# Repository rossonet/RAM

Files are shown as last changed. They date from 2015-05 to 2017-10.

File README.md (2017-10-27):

# Rossonet Atom Machine

Rossonet



[http://www.rossonet.org](http://www.rossonet.org)

Licenza: [LGPL 3.0](https://www.gnu.org/licenses/lgpl.html)
Per maggiori dettagli sulla licenza rimando a [questa voce](http://it.wikipedia.org/wiki/GNU_Lesser_General_Public_License) di Wikipedia

LGPL Logo

Rossonet Atom Machine è una macchina a controllo numerico su 3 assi completamente open source.

La macchina è governabile via rete tramite un browser, il software montato a bordo guida l'utente nelle varie fasi di lavorazioni in un contesto social.

La macchina è composta da parti in plastica derivate da varie versione della [RepRap Rostock](http://reprap.org/wiki/Rostock) e componenti meccaniche (barre rettificate, cuscinetti e cinghie) facilmente reperibili localmente e online. Tutte le parti sono disegnate [con OpenScad](http://www.openscad.org/).

I giunti cardanici sono magnetici, questo permette una rapida sostituzione delle parti, ma anche la sicurezza che, in caso di errore nella programmazione software, la macchina si smonterà senza danneggiarsi o danneggiare qualcuno o qualcosa.
 
L'elettronica di controllo è una [Megatronics V3](http://reprapworld.com/mt/megatronics3_src.zip), architettura che integra in un'unica scheda il progetto Arduino Mega e il progetto RAMPS. La scheda monta un processore Atmega2560 a 16MHz.

L'elettronica è governata dal [firmware Marlin](https://github.com/MarlinFirmware/Marlin).

Alla scheda di controllo è collegato un computer embedded con processore A20. Sui protipi è montata una scheda [BananaPI](http://www.bananapi.org/).

Oltre ad una distribuzione Linux ottimizzata per la scheda specifica -Fedora 22-, il computer offre le fuzionalità di controllo web tramite [OctoPrint](http://octoprint.org/); la virtualizzazione della seriale, per usare la macchina come una CNC con programmi come [Printrun](https://github.com/kliment/Printrun) o [LinuxCNC](http://sourceforge.net/projects/emc/); le funzionalità di slicing per la stampa plastica sono gestite con [CuraEngine](https://github.com/Ultimaker/CuraEngine); le funzionalità CAD con [OpenJSCAD](https://github.com/Spiritdude/OpenJSCAD.org/wiki/User-Guide); il CAM (calcolo dei percorsi di incisione o scrittura) con [PyCAM](http://pycam.sourceforge.net/).

L'interfaccia web è fruibile da dispositivo mobile grazie alla libreria [Twitter Bootstrap](http://getbootstrap.com/2.3.2/).

<a href="http://www.youtube.com/watch?feature=player_embedded&v=1BcRuSaGWxI" target="_blank">Rossonet</a>

## Funzionalità
1. stampa 3D a filamento fuso (1,75mm) con temperatura di lavorazione fino 240 gradi (PLA,ABS,ecc...);
2. attuatore per eseguire GCODE con penne, matite, pennarelli, ecc...;
3. interfaccia web responsible;
4. taglio polistirolo -da implementare-;
5. piano di lavoro riscaldato con aggancio magnetico -da implementare-;
6. attuatore a siringa per la lavorazione di materiali liquidi -da implementare-;
7. help Online integrato nell'interfaccia per imparare con il supporto multimediale come utilizzare e svolgere le procedure di manutenzione della macchina -in sviluppo-. In particolare le procedure di calibrazione della struttura, calibrazione del termostato, cambio filamento, tuning z-probe;
8. sistema di assistenza remoto basato su chat web -integrazione Olark-;
9. integrazione software di modellizazione parametrica con libreria online in OpenJScad -da implementare-;
10. imballaggi per il traporto -da implementare-;
11. API per l'interfaccia di software di terze parti;
12. integrazione MQTT per il monitoraggio integrato nelle reti IoT -da implementare-;
13. integrazione piattaforma [Rossonet Ar4k](https://github.com/rossonet/agenteAr4k);
14. connessione ethernet o wifi (tramite plug usb);
15. slicing sampa plastica integrato con [CuraEngine](https://github.com/Ultimaker/CuraEngine);
16. timelaps automatico.

## Versioni
Attualmente sistono due versioni preconfigurate della macchina. La versione "T" con le parti meccaniche realizzate in officina di precisione e il modello Eroina studiato per essere realizzabile partendo da stampe plastiche di piccole dimensioni. 

### Versione Eroina (bootstrap progetto)
La versione Eroina è composta da una struttura realizzata in carpenteria (legno, metallo o altre strutture ricavate con il materiale disponibile) e da parti stampate in plastica con sagome inferiori ai 15cm per ogni dimensione. Il nostro primo prototipo è stato stampato con un [Arduino Materia 101](https://www.arduino.cc/en/Main/ArduinoMateria101).

[Schema assemblaggio generale](https://github.com/rossonet/RAM/blob/master/parti/stl/eroina/assemblaggio.stl)

#### Video fasi studio prototipo
studio z-probe
<a href="http://www.youtube.com/watch?feature=player_embedded&v=OmTOs6jjuCw" target="_blank">Rossonet</a>

primi test scheda controllo
<a href="http://www.youtube.com/watch?feature=player_embedded&v=n3oExDMJfP0" target="_blank">Rossonet</a>

primo assemblaggio struttura
<a href="http://www.youtube.com/watch?feature=player_embedded&v=B5Mmt7lzHgg" target="_blank">Rossonet</a>

test usb over ethernet
<a href="http://www.youtube.com/watch?feature=player_embedded&v=iVD2OGaxWTA" target="_blank">Rossonet</a>

esperimenti Marlin
<a href="http://www.youtube.com/watch?feature=player_embedded&v=0e1HDMZBxl4" target="_blank">Rossonet</a>

esperimenti con Marlin
<a href="http://www.youtube.com/watch?feature=player_embedded&v=ZnjUfesXWaY" target="_blank">Rossonet</a>

test GCODE con biglie
<a href="http://www.youtube.com/watch?feature=player_embedded&v=iLzKpcrZ054" target="_blank">Rossonet</a>

primi esperimenti scrittura con pennarello
<a href="http://www.youtube.com/watch?feature=player_embedded&v=tii90TnvsTo" target="_blank">Rossonet</a>

stampa plastica
<a href="http://www.youtube.com/watch?feature=player_embedded&v=GQly_ISp1_0" target="_blank">Rossonet</a>

#### Elenco materiali elettronici, movimentazione lineare e hot end 
1. [E3D v6 HotEnd Full Kit - 1.75mm Universal (Direct) (24v)](http://e3d-online.com/E3D-v6/Full-Kit?product_id=380);
2. ventola raffreddamento 30mmx30mmx10mm 12V;
3. [Banana PI](http://www.bananapi.org/p/product.html);
4. [Megatronics V3](http://reprapworld.com/?products_details&products_id/468/cPath/1591_1643);
5. 4 x [ponti H -DRV8825 Stepper Motor Driver Carrier-](https://www.pololu.com/product/2132);
6. 4 x NEMA17 Stepper motor 1,8 gradi/step - 4,8kg/cm;
7. 3 x [endstop meccanici](http://www.elecfreaks.com/store/images/Mech_Endstop-D.jpg);
8. telecamera USB compatibile con Fedora 22 su Banana PI;
9. servo motore z-probe: 9G micro servo;
10. micro pulsante PCB 3mmx3.5mmx1.8mm button switch (per z-probe);
11. 6 x barre rettificate da 1mt x 12mm;
12. 6 x cuscinetti lineari a sfera LM12UU;
13. cuscinetto piccolo estrusore;
14. cuscinetto grande estrusore;
15. 3 x cuscinetti fine corsa;
13. ~7mt cinghia trasmissione 6mm (GT2 -passo 2mm-);
14. 3 x pulegge alluminio 20 denti (GT2 -passo 2mm-);
15. ~6mt cavo di rete UTP -da utilizzare per i cablaggi-;
16. ~3mt cavo bipolare per resistenza hotend;
17. fascette varie;
18. spinotti per Megatronics v3 (4 stepper, 2 ventole, 3+1 endstop -comprende servo-);
19. alimentatore 12V da PC;
20. scheda SD da 16GB per Banana PI;
21. scheda microSD per memoria tampone scheda controllo;
22. cavo USB da maschio A a maschio B per connessione tra Banana PI e Megatronics v3;
23. terminale maschio micro USB per alimentazione Banana PI. 

#### Elenco materiale stampato
1. 3 x [blocco motore](https://github.com/rossonet/RAM/blob/master/parti/stl/eroina/blocco_motore_v1.stl);
2. 3 x [rimando cinghia](https://github.com/rossonet/RAM/blob/master/parti/stl/eroina/fine_corsa.stl);
3. 3 x [carrello](https://github.com/rossonet/RAM/blob/master/parti/stl/eroina/carrello.stl);
4. 3 x [tensionatore](https://github.com/rossonet/RAM/blob/master/parti/stl/eroina/Belt-Tensioner-V1.stl);
5. 3 x [supporto endstop](https://github.com/rossonet/RAM/blob/master/parti/stl/eroina/supporto_endstop.stl);
6. 1 x [attuatore](https://github.com/rossonet/RAM/blob/master/parti/stl/eroina/piattaforma_3dprint_v2.stl): [base](https://github.com/rossonet/RAM/blob/master/parti/stl/eroina/piattaforma_3dprint_v2_base.stl), [coperchio "A"](https://github.com/rossonet/RAM/blob/master/parti/stl/eroina/piattaforma_3dprint_v2_coperchio_a.stl), [coperchio "B"](https://github.com/rossonet/RAM/blob/master/parti/stl/eroina/piattaforma_3dprint_v2_coperchio_b.stl), [braccio z-probe](https://github.com/rossonet/RAM/blob/master/parti/stl/eroina/piattaforma_3dprint_v2_zprobe.stl);
7. [estrusore](https://github.com/rossonet/RAM/blob/master/parti/stl/eroina/airtripper-extruder-v3.stl);
8. [attuatore pennarelli](https://github.com/rossonet/RAM/blob/master/parti/stl/eroina/piattaforma_giotto_turbocolor.stl) collaudato con "[Giotto Turbocolor](http://www.fila.it/giotto/prodotti/pennarelli/giotto-turbo-color)" con [questo supporto](https://github.com/rossonet/RAM/blob/master/parti/stl/eroina/supporto_giotto_turbocolor.stl).

#### Elenco materiale per struttura e piccola ferramenta
Il progetto di questa versione prevede la predisposizione delle tre colonne attive su una struttura portante realizzata artigianalmente. Lo schema di montaggio generale è visionabile [qui](https://github.com/rossonet/RAM/blob/master/parti/stl/eroina/assemblaggio.stl). La struttura deve garantire una sufficiente rigidità, attenuare le vibrazioni dei movimenti con adeguati piedi e/o ammortizzatori.

La struttura può essere realizzata con diametro a piacere tra i 47 e i 70 centimetri. Al diminuire del diametro proporzianalmete diminuiscono i bracci diagonali dell'attuatore, aumenta l'altezza e diminuisce il raggio utile per la stampa. Per esempio nella [configurazione con raggio di 23,5cm](http://www.rossonet.org/dati/RAM235.html) si ottiene un area di stampa cilindrica con un raggio di 19,5cm e altezza di 43,5cm, i bracci diagonali sono lunghi 395mm. Nella [configurazione con raggio di 35cm](http://www.rossonet.org/dati/RAM350.html) il cilindro utile ha raggio di 31cm e altezza di 20,5cm, i bracci sono lunghi 625mm. 

1. 3 x ferramenta fine corsa;
2. 3 x ferramenta blocco motore;
3. ferramenta attuatore;
4. ferramenta estrusore;
4. 6 x magneti carrello;
5. 12 x magneti attuatore;
6. 12 x sfere acciaio 12mm;
7. 12 x supporti distanziatori in plastica per magneti -da verificare-;
8. 6 x bacchette alluminio diametro 10mm lunghezza da 39,5cm a 62,5cm -a seconda del raggio della struttura portante-;

#### Fasi assemblaggio
-to do-
...con foto in archivio git

#### Servizi
1. download firmware per Banana PI -to do-
2. vendita online modello "T"
3. plastiche "Eroina"
4. elettronica e materiale vario "Eroina"

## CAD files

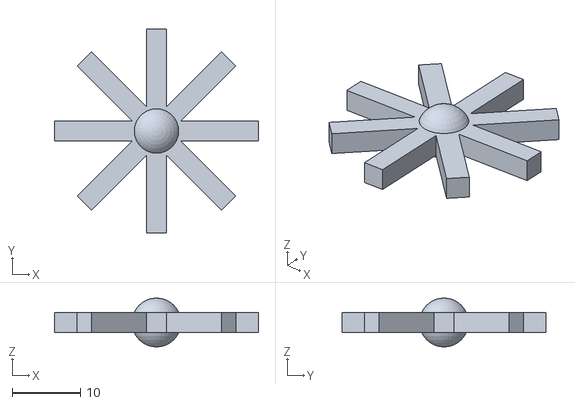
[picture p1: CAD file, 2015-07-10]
OpenJSCAD.org-master/examples/include-test/main.stl
30.0 x 30.0 x 7.20

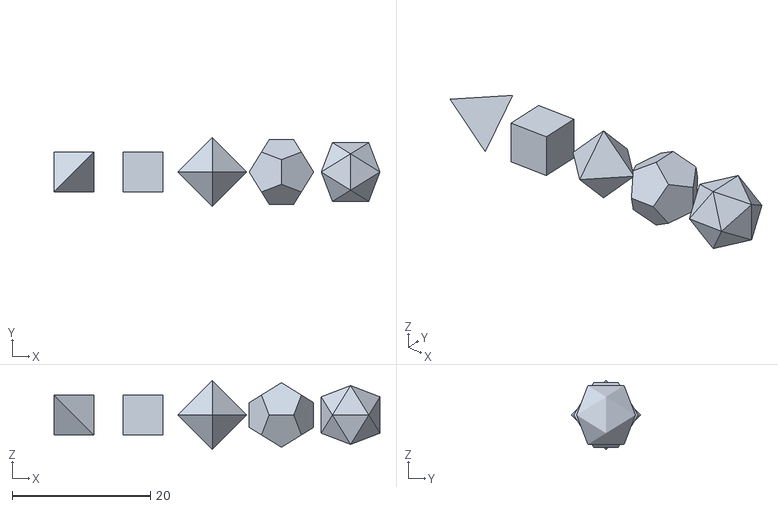
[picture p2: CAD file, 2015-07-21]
OpenJSCAD/examples/platonics/main.stl
47.1 x 10.0 x 10.0

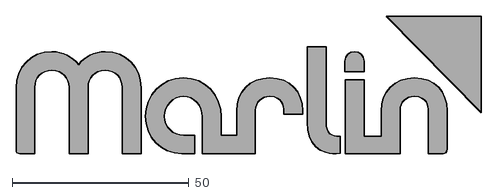
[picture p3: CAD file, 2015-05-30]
Marlin/Documentation/Logo/Marlin Logo.dxf
131.6 x 39.5

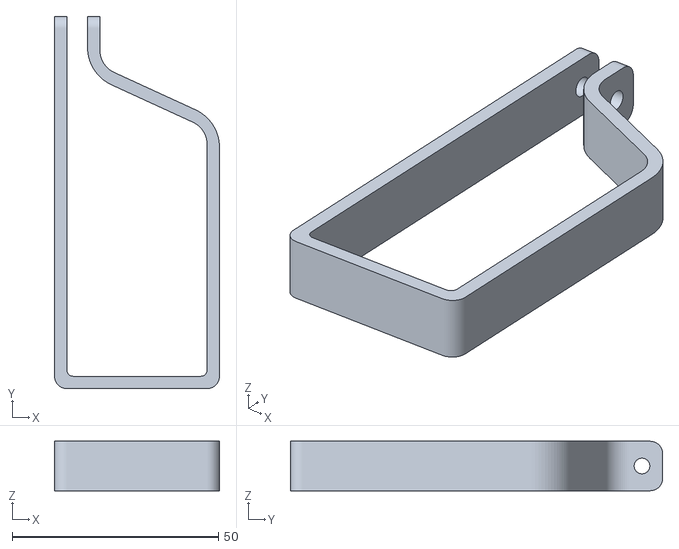
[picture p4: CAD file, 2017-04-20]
modelli/progetti/plotter_a_corde/files/FCE.1501.03.006_batteryholder_side.STL
40.0 x 90.2 x 12.0

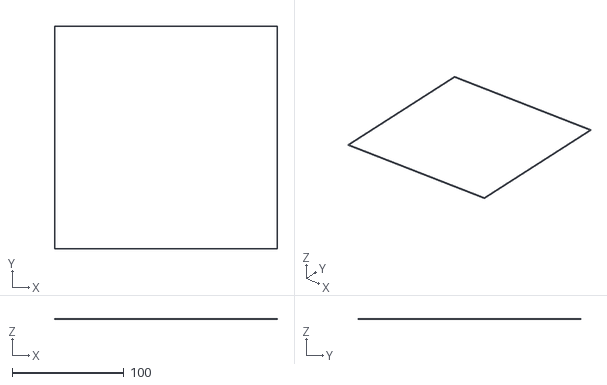
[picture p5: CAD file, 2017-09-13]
modelli/test2d/quadrato_20.stl
200.0 x 200.0 x 1.00

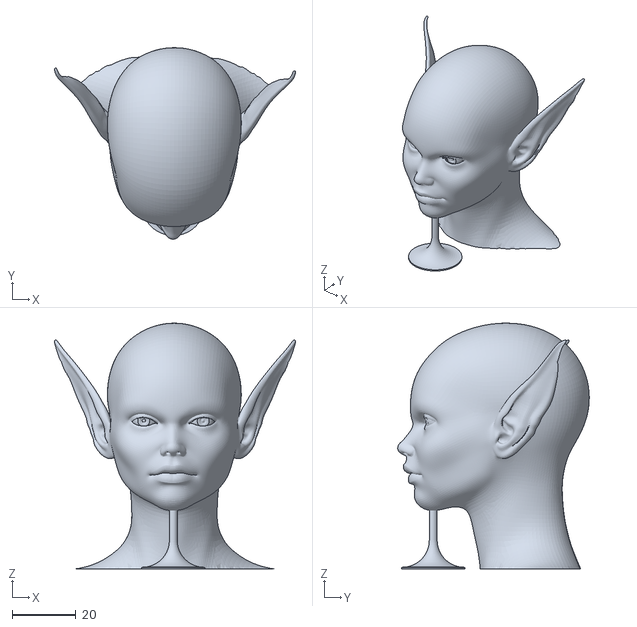
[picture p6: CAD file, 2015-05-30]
modelli/test3d/elfgirl_support_V1.stl
75.8 x 60.3 x 77.3

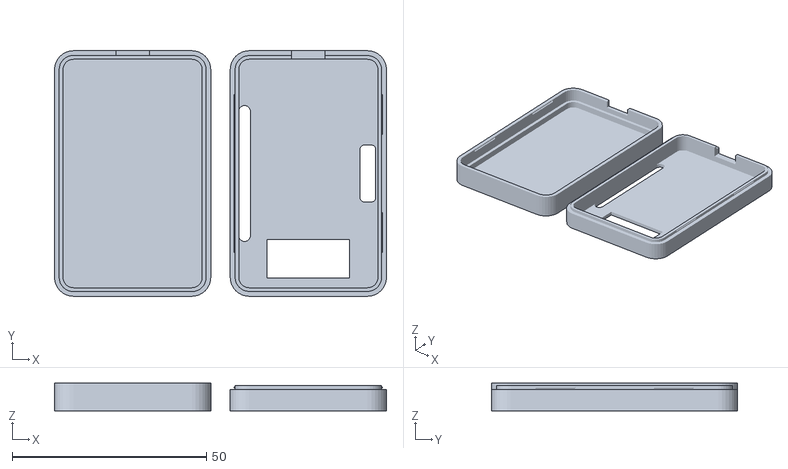
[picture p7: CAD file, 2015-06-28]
OctoPrint/tests/filemanager/_files/bp_case.stl
85.5 x 63.2 x 7.15

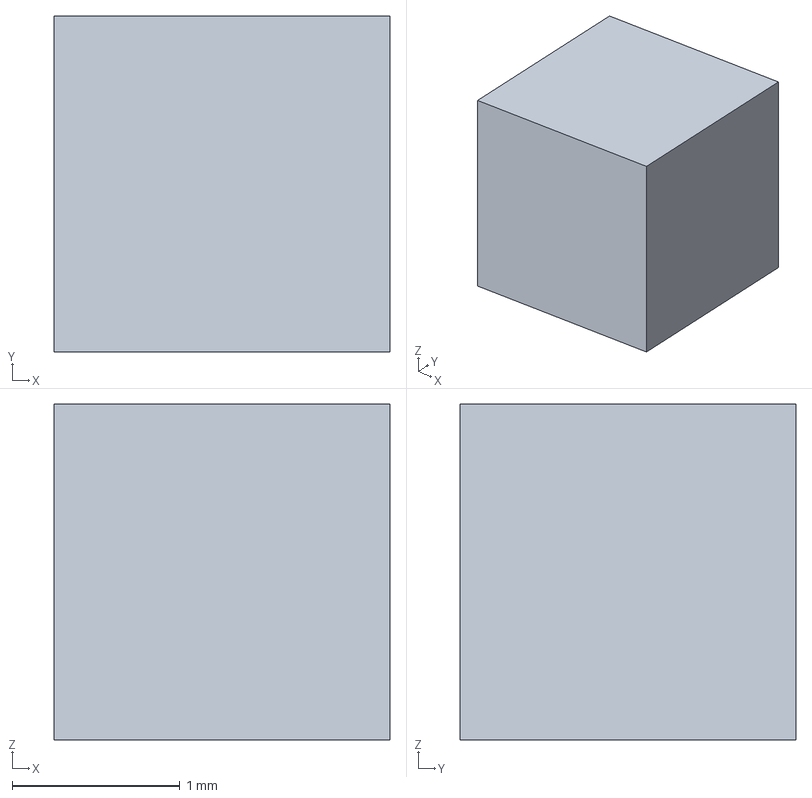
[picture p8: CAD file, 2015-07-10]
OpenJSCAD.org-master/examples/amf/Amf_Cube.amf
2.00 x 2.00 x 2.00 mm

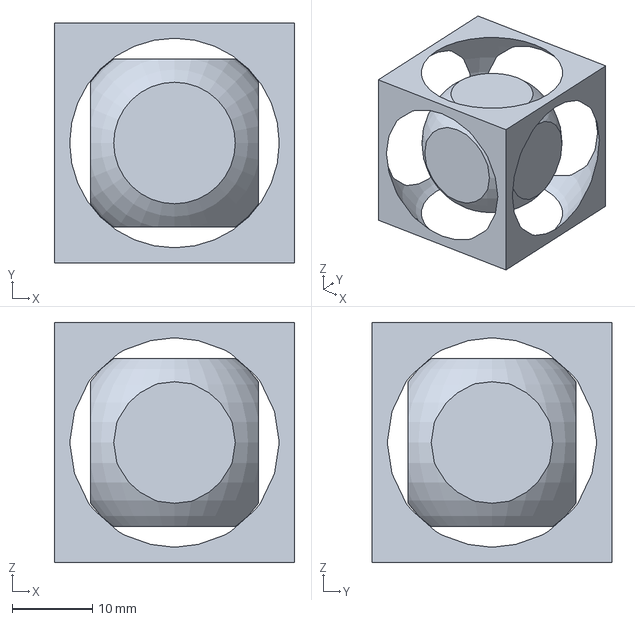
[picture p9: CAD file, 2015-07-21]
OpenJSCAD.org-master/examples/logo.amf
30.0 x 30.0 x 30.0 mm

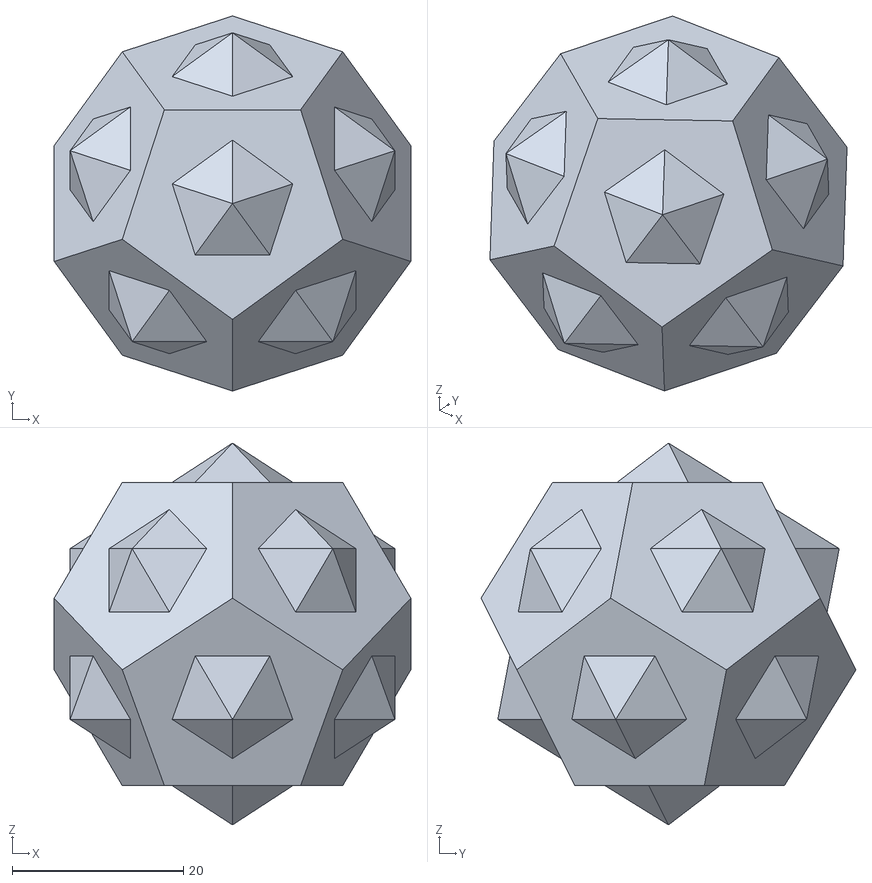
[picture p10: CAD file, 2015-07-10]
OpenJSCAD.org-master/examples/platonics/origv07/dualdodeca_union.stl
41.6 x 43.7 x 44.5

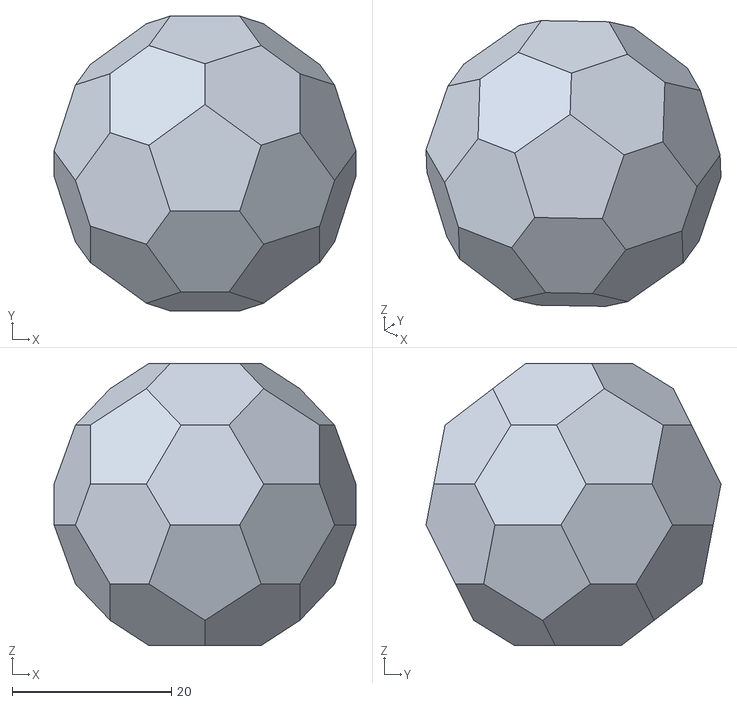
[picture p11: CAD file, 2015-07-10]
OpenJSCAD/examples/platonics/origv07/dualdodeca_intersection.stl
37.9 x 37.0 x 35.4

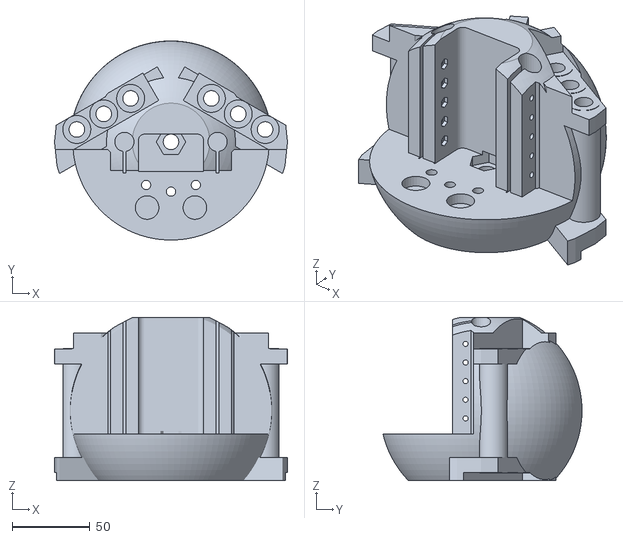
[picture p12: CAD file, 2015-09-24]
parti/stl/piede.stl
150.0 x 128.1 x 105.0

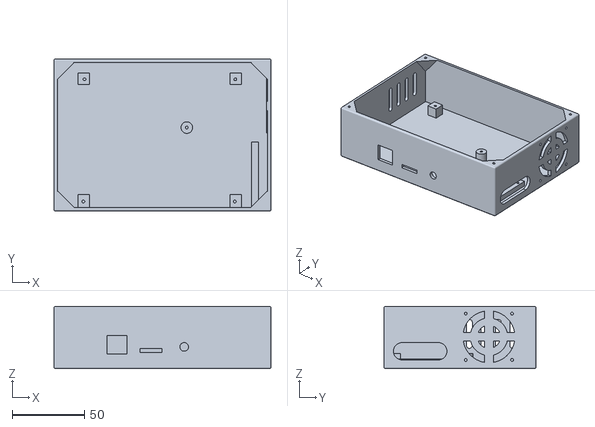
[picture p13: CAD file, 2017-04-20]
RAM/scad/megatronics_case.stl
150.0 x 105.0 x 43.0

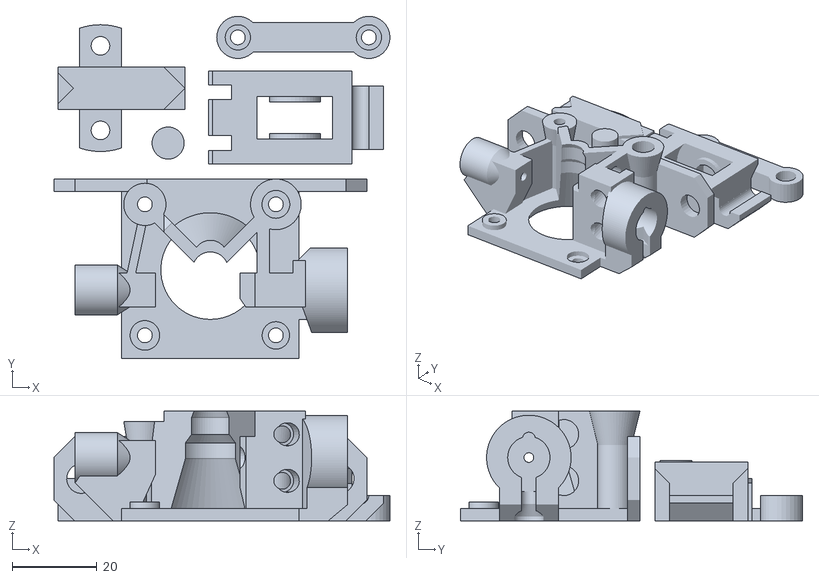
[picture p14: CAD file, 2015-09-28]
RAM/stl/eroina/airtripper-extruder-v3.stl
79.5 x 81.0 x 26.0

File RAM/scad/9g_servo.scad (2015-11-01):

9g_motor();

module 9g_motor(){
	difference(){			
		union(){
			color("steelblue") cube([23,12.5,22], center=true);
			color("steelblue") translate([0,0,5]) cube([32,12,2], center=true);
			color("steelblue") translate([5.5,0,2.75]) cylinder(r=6, h=25.75, $fn=20, center=true);
			color("steelblue") translate([-.5,0,2.75]) cylinder(r=1, h=25.75, $fn=20, center=true);
			color("steelblue") translate([-1,0,2.75]) cube([5,5.6,24.5], center=true);		
			color("white") translate([5.5,0,3.65]) cylinder(r=2.35, h=29.25, $fn=20, center=true);				
		}
		translate([10,0,-11]) rotate([0,-30,0]) cube([8,13,4], center=true);
		for ( hole = [14,-14] ){
			translate([hole,0,5]) cylinder(r=2.2, h=4, $fn=20, center=true);
		}	
	}
}

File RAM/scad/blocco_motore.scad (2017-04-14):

use <Write.scad>
use <modulo.scad>
use <nema_17.scad>

//write("Rossonet RAM",h=5,t=3);

//distanza barre
w=60;
wall_t=5;
hole_dia=3;
cut_in=1;
holder_h=16.5;
rod_distance=50;
rod_dia=11.5;
wall_w=rod_distance-(rod_dia/2);
$fn=240;

module vite() {
  for (x = [-w/2, w/2]) {
    translate([x, 0, 0]) {
	 // Push-through M3 screw hole.
      translate([0, -10, 0]) rotate([0, 90, 0]) cylinder(r=1.65, h=20, center=true, $fn=90); 
	 // M3 nut holder.
      translate([-x/3.8, -10, 0]) rotate([0, 90, 0]) cylinder(r=3.2, h=2.3, center=true, $fn=6);  //rotate([30, 0, 0]) 
    }
  }
}

module agganci() {
    m = 29;
    translate([0, 0, 0]) {
        rotate([90, 0, 0]) cylinder(r=13, h=40, center=true, $fn=48);
        cube([12, 40, 12], center=true);
        // Motor mounting screw slots
        translate([m/2, 0, m/2]) rotate([0, -45, 0])
        cube([9, 40, 3], center=true);
        translate([-m/2, 0, m/2]) rotate([0, 45, 0])
        cube([9, 40, 3], center=true);
        translate([m/2, 0, -m/2]) rotate([0, 45, 0])
        cube([9, 40, 3], center=true);
        translate([-m/2, 0, -m/2]) rotate([0, -45, 0])
        cube([9, 40, 3], center=true);
    }
    for (z = [-36,-24, -12, 0, 12, 24]) {
      translate([0, 0, z]) vite();
    }
    
}

// Scasso pannello plexiglass
module plexiglass(){
    difference(){
        cylinder(r=80,h=58,center=true);
        union() {
            cylinder(r=60,h=60,center=true);
            translate([0, 34, 0])cube([200,100,60],center=true);
        }
    }
    for (altezza = [0,14,-14]) {
        for (angolo = [70,62,54,-70,-62,-54]) {
            rotate([90,0,angolo])
                translate([0,altezza,50])
                    cylinder(r=0.7,h=12);
        }
    }
    for (altezza = [27.5,-27.5]) {
        for (angolo = [70,62,54,-70,-62,-54,0,20,-20,40,-40]) {
            rotate([90,0,angolo])
                translate([0,altezza,50])
                    cylinder(r=0.7,h=12);
        }
    }
}

// passacavi switch fine corsa
module cavetti() {
    intersection() {
        cube([80,80,80]);
        difference(){
            cylinder(r=61,h=6);
            translate([0,0,-1])cylinder(r=56,h=8);
        }
    }
}

module blocco_motore() {
    difference(){
        // sfera base
        union(){
            sphere(r=70,center=true);
            //translate([0, 0, 6])sphere(r=66,center=true);
            //translate([0, 0, -6])sphere(r=66,center=true);
            struttura_esterna();
        }
        // SOTTRAZIONE
        union(){
            // sagoma motore
            translate([0, 35, 0])  cube([80,50,50],center=true);
            // pannellino
            rotate([0,0,180])translate([0, 1, 0])plexiglass();
            // vuoto corpo motore
            difference() {
                union(){
                    translate([24, 0, 0]) sphere(r=34,center=true);
                    translate([-24, 0, 0]) sphere(r=34,center=true);
                }
                translate([0, -20, 0])
                cube([300,60,300],center=true);
            }
            // scasso lineare
            translate([0,0,-60])scasso_lineare();
            // taglio frontale
            translate([0,-58.5,0])
            cube([200,80,200],center=true);
            // aggancio motore e viti barre
            agganci();
            // passacavo di rete
            translate([-20,25,-30])
            cylinder(r=5,h=40,center=true);
            // passacavo sensore
            //translate([-5,-18,-20])cavetti();
            // scasso bulloni barra
            translate([59,-15,-6])
            difference(){
                cube([40,20,80],center=true);
                translate([-22,12,0])
                cylinder(r=4,h=100,center=true);
            }
            translate([-59,-15,-6])
            difference(){
                cube([40,20,80],center=true);
                translate([22,12,0])
                cylinder(r=4,h=100,center=true);
            }
            // parte bassa
            translate([0,0,-65])
            cube([160,160,40],center=true);
            // bullone aggancio superiore (M8)
            translate([0,0,40])
            cylinder(r=5,h=100,center=true);
            translate([0,0,34])
            cylinder(r=9.5,h=8,center=true,$fn=6);
            // struttura
            struttura();
            
        }
    }
}

module scasso_lineare() {
   h=200;
   for (x = [-w/2, w/2]) {
      translate([x, 0, 0]) {
		cylinder(r=6.2, h=h+1, center=true);
		translate([0, -10, 0]) cube([2, 20, h+1], center=true);
      }
    }
    // Belt path.
    translate([0, -5, -10]) cube([w-25, 20, h+1], center=true);
    translate([0, -9, -10]) cube([w-18, 20, h+1], center=true);
    translate([-w/2+13, 1, -10]) cylinder(r=4, h=h+1, center=true);
    translate([ w/2-13, 1, -10]) cylinder(r=4, h=h+1, center=true);
}


module barre(){
    rotate([180,0,30])translate([26,250,0])cube([20.4,500,20.4],center=true);
    rotate([180,0,-30])translate([-26,250,0])cube([20.4,500,20.4],center=true);
}

module barre_esterno(){
    rotate([180,0,30])translate([21,50,0])cube([28,120,20],center=true);
    rotate([180,0,-30])translate([-21,50,0])cube([28,120,20],center=true);
}

module struttura(){
    translate([0,40,50])barre();
    translate([0,40,-50])barre();
}

module struttura_esterna(){
    difference(){
        union(){
            translate([0,40,40])barre_esterno();
            translate([0,40,-40])barre_esterno();
        }
        union(){
            struttura();
            translate([0,-80,0])
            cube([200,200,200],center=true);
        }
    }
}

module passante(){
    difference(){
        cylinder(r=9,h=80,center=true);
        cylinder(r=5,h=82,center=true);
    }
    
}

module passanti() {
    translate([0,90,0]){
        rotate([0,0,30])
        translate([0,-64,0])passante();
        rotate([0,0,-30])
        translate([0,-64,0])passante();
        rotate([0,0,30])
        translate([0,-84,0])passante();
        rotate([0,0,-30])
        translate([0,-84,0])passante();
        rotate([0,0,30])
        translate([0,-104,0])passante();
        rotate([0,0,-30])
        translate([0,-104,0])passante();
    }
}

module fori_m8() {
        translate([0,90,0]){
        rotate([0,0,30])
        translate([0,-64,0])
            cylinder(r=5,h=86,center=true);
        rotate([0,0,-30])
        translate([0,-64,0])
            cylinder(r=5,h=86,center=true);
        rotate([0,0,30])
        translate([0,-84,0])
            cylinder(r=5,h=86,center=true);
        rotate([0,0,-30])
        translate([0,-84,0])
            cylinder(r=5,h=86,center=true);
        rotate([0,0,30])
        translate([0,-104,0])
            cylinder(r=5,h=86,center=true);
        rotate([0,0,-30])
        translate([0,-104,0])
            cylinder(r=5,h=86,center=true);
            translate([0,-72.5,0])cube([85,10,40],center=true);
    }
}

module testa(){
    difference(){
        union(){
            blocco_motore();
            passanti();
            rotate([180,180,0])translate([0,8,-45])wall();
        }
        fori_m8();
    }
}


module hole(){
	rotate([90,0,0]){
		cylinder(r=hole_dia/2,h=wall_t*2, center=true);
		if (cut_in==1) {
			cylinder(r1=0,r2=hole_dia*0.6,h=wall_t*1.01,center=true);
		}
	}
}

module fillet(r, h) {
    translate([r / 2, r / 2, 0])

        difference() {
            cube([r + 0.01, r + 0.01, h], center = true);

            translate([r/2, r/2, 0])
                cylinder(r = r, h = h + 1, center = true);

        }
}


module wall(){
	difference(){
		translate([0,8.2,holder_h/2]){
				difference(){
				cube([wall_w+12,wall_t,holder_h],center=true);
				translate([(wall_w+12)/2,3,0]){
					rotate([0,0,180]) {
						fillet(5,holder_h+2);
					}
				};
				translate([-(wall_w+12)/2,3,0]){
					rotate([0,0,270]) {
						fillet(5,holder_h+2);
					}
				}
				}
		}
		union(){
                translate([18,8.2,3]){
                    hole();	
                }
                translate([-2,8.2,3]){
                    hole();	
                }
                translate([-16.5,8.2,3]){
                    hole();	
                }
                translate([-16.5,8.2,14]){
                    hole();	
                }
			}
    }
}
  
// Struttura profilati quadrati 20mm
//#struttura();
// Motore
//translate([0, 10, 0])rotate([90,0,0])nema_17();
// Blocco
testa();
//fori_m8();
//plexiglass();

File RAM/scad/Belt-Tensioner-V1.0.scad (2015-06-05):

// Enlarged Rostock Belt tensioner
//    - T2.5 self locking belt geometry based on belt_coupler_v6 from Okatake


// Rostock Motor End from Jcrocholl modified by Kolergy to:
//    - Take 12x1000mm smooth rods and KB-12-WW Linear Bearings
//    - Increased base height to locate electronics below the base
//    - Stand on three feets
use <belt_coupler_v6_Mod.scad>
use <carrello.scad>

motor_end_height      =  64;  // Was 44
idler_end_height      =  28;
carriage_height       =  32; // Adapted to cover full length +2 of the Linear bearing
platform_thickness    =   8;
bed_thickness         =  12;
pcb_thickness         =   2;
smooth_rod_length     =1000;
platform_hinge_offset =  33;
carriage_hinge_offset =  22;
tower_radius          = 300;
rod_length            = tower_radius * 1.44;

H  = carriage_height;
th = 4;

//%carriage();

	difference() {
union(){
	translate([7.5, 5., 0]) cube([15, 5., 12], center=true);
		translate([7.5, 1, 0]) cube([15, 7, 12], center=true);
}
		translate([8, 0, 7.5]) rotate([-45, 0,  0]) cube([17, 5, 15], center=true);
		translate([ 7.5, 3.5, -(H+th)/2+0.5]) rotate([90, -90, 0]) belt();
		translate([ 8.0, 3.5, -(H+th)/2+0.6]) rotate([90, -90, 0]) belt(); // Slightly enlarge the gap of the belt
		translate([12, 0, 0]) cylinder(r=1.6, h=H+th+2, center=true, $fn=12);
		translate([ 3.5, 0, 0]) cylinder(r=1.6, h=H+th+2, center=true, $fn=12);
		translate([12, 0, -7]) cylinder(r=3.3, h=4, center=true, $fn=6);
		translate([ 3.5, 0, -7]) cylinder(r=3.3, h=4, center=true, $fn=6);
	
}

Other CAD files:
OpenJSCAD/examples/amf/VertColors.amf
RAM/stl/fine_corsa.stl
RAM/scad/belt_coupler_v6_Mod.scad
OctoPrint/tests/filemanager/_files/crazyradio.stl
OpenJSCAD.org-master/examples/3d_sculpture-VernonBussler.stl
OpenJSCAD.org-master/examples/amf/CurveEdgeTest.amf
OpenJSCAD.org-master/examples/amf/Rook.amf
OpenJSCAD.org-master/examples/amf/Sphere20Face.amf
OpenJSCAD.org-master/examples/amf/VertColors.amf
OpenJSCAD.org-master/examples/example001.scad
OpenJSCAD.org-master/examples/example002.scad
OpenJSCAD.org-master/examples/example003.scad
OpenJSCAD.org-master/examples/example004.scad
OpenJSCAD.org-master/examples/example005.scad
OpenJSCAD.org-master/examples/frog-OwenCollins.stl
OpenJSCAD.org-master/examples/platonics/origv07/dualdodeca_difference.stl
OpenJSCAD.org-master/examples/platonics/origv07/maths_geodesic.scad
OpenJSCAD.org-master/examples/platonics/origv07/platonic.scad
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

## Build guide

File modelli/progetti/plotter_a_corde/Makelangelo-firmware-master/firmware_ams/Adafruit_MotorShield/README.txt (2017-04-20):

 This is the library for the Adafruit Motor Shield V2 for Arduino.
 It supports DC motors & Stepper motors with microstepping as well
 as stacking-support. It is *not* compatible with the V1 library!

 It will only work with https://www.adafruit.com/products/1483

 Adafruit invests time and resources providing this open
 source code, please support Adafruit and open-source hardware
 by purchasing products from Adafruit!

 Written by Limor Fried/Ladyada for Adafruit Industries.
 BSD license, check license.txt for more information.
 All text above must be included in any redistribution.

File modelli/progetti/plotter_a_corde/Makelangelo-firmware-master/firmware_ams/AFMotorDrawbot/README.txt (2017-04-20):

This is the August 12, 2009 Adafruit Motor shield firmware with basic Microstepping support. Works with all Arduinos and the Mega

For more information on the shield, please visit http://www.ladyada.net/make/mshield/

To install, click DOWNLOAD SOURCE in the top right corner, and see our tutorial at http://www.ladyada.net/library/arduino/libraries.html on Arduino Library installation

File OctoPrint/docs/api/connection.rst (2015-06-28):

.. _sec-api-connection:

*******************
Connection handling
*******************

.. contents::

.. _sec-api-connection-current:

Get connection settings
=======================

.. http:get:: /api/connection

   Retrieve the current connection settings, including information regarding the available baudrates and
   serial ports and the current connection state.

   **Example**

   .. sourcecode:: http

      GET /api/connection HTTP/1.1
      Host: example.com
      X-Api-Key: abcdef...

   .. sourcecode:: http

      HTTP/1.1 200 OK
      Content-Type: application/json

      {
        "current": {
          "state": "Operational",
          "port": "/dev/ttyACM0",
          "baudrate": 250000,
          "printerProfile": "_default"
        },
        "options": {
          "ports": ["/dev/ttyACM0", "VIRTUAL"],
          "baudrates": [250000, 230400, 115200, 57600, 38400, 19200, 9600],
          "printerProfiles": [{"name": "Default", id: "_default"}],
          "portPreference": "/dev/ttyACM0",
          "baudratePreference": 250000,
          "printerProfilePreference": "_default",
          "autoconnect": true
        }
      }

   :statuscode 200: No error

.. _sec-api-connection-command:

Issue a connection command
==========================

.. http:post:: /api/connection

   Issue a connection command. Currently available command are:

   connect
     Instructs OctoPrint to connect to the printer. Additional parameters are:

     * ``port``: Optional, specific port to connect to. If not set the current ``portPreference`` will be used, or if
       no preference is available auto detection will be attempted.
     * ``baudrate``: Optional, specific baudrate to connect with. If not set the current ``baudratePreference`` will
       be used, or if no preference is available auto detection will be attempted.
     * ``printerProfile`` Optional, specific printer profile to use for connection. If not set the current default printer
       profile will be used.
     * ``save``: Optional, whether to save the request's ``port`` and ``baudrate`` settings as new preferences. Defaults
       to ``false`` if not set.
     * ``autoconnect``: Optional, whether to automatically connect to the printer on OctoPrint's startup in the future.
       If not set no changes will be made to the current configuration.

   disconnect
     Instructs OctoPrint to disconnect from the printer.

   fake_ack
     Fakes an acknowledgement message for OctoPrint in case one got lost on the serial line and the communication
     with the printer since stalled. This should only be used in "emergencies" (e.g. to save prints), the reason
     for the lost acknowledgement should always be properly investigated and removed instead of depending on this
     "symptom solver".

   **Example Connect Request**

   .. sourcecode:: http

      POST /api/connection HTTP/1.1
      Host: example.com
      Content-Type: application/json
      X-Api-Key: abcdef...

      {
        "command": "connect",
        "port": "/dev/ttyACM0",
        "baudrate": 115200,
        "printerProfile": "my_printer_profile",
        "save": true,
        "autoconnect": true
      }

   .. sourcecode:: http

      HTTP/1.1 204 No Content

   **Example Disconnect Request**

   .. sourcecode:: http

      POST /api/connection HTTP/1.1
      Host: example.com
      Content-Type: application/json
      X-Api-Key: abcdef...

      {
        "command": "disconnect"
      }

   .. sourcecode:: http

      HTTP/1.1 204 No Content

   **Example FakeAck Request**

   .. sourcecode:: http

      POST /api/connection HTTP/1.1
      Host: example.com
      Content-Type: application/json
      X-Api-Key: abcdef...

      {
        "command": "fake_ack"
      }

   .. sourcecode:: http

      HTTP/1.1 204 No Content

   :json string command:      The command to issue, either ``connect``, ``disconnect`` or ``fake_ack``.
   :json string port:         ``connect`` command: The port to connect to. If left out either the existing ``portPreference``
                              will be used, or if that is not available OctoPrint will attempt auto detection. Must be part
                              of the available ports.
   :json number baudrate:     ``connect`` command: The baudrate to connect with. If left out either the existing
                              ``baudratePreference`` will be used, or if that is not available OctoPrint will attempt
                              autodetection. Must be part of the available baudrates.
   :json string printerProfile: ``connect`` command: The id of the printer profile to use for the connection. If left out the current
                                default printer profile will be used. Must be part of the available printer profiles.
   :json boolean save:        ``connect`` command: Whether to save the supplied connection settings as the new preference.
                              Defaults to ``false`` if not set.
   :json boolean autoconnect: ``connect`` command: Whether to attempt to automatically connect to the printer on server
                              startup. If not set no changes will be made to the current setting.
   :statuscode 204:           No error
   :statuscode 400:           If the selected `port` or `baudrate` for a ``connect`` command are not part of the available
                              options.

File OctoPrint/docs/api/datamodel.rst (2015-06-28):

.. _sec-api-datamodel:

*****************
Common data model
*****************

.. contents::

.. _sec-api-datamodel-printer:

Printer related
===============

.. _sec-api-datamodel-printer-state:

Printer State
-------------

.. list-table::
   :widths: 15 5 10 30
   :header-rows: 1

   * - Name
     - Multiplicity
     - Type
     - Description
   * - ``text``
     - 1
     - String
     - A textual representation of the current state of the printer, e.g. "Operational" or "Printing"
   * - ``flags``
     - 1
     - Printer state flags
     - A couple of boolean printer state flags
   * - ``flags.operational``
     - 1
     - Boolean
     - ``true`` if the printer is operational, ``false`` otherwise
   * - ``flags.paused``
     - 1
     - Boolean
     - ``true`` if the printer is currently paused, ``false`` otherwise
   * - ``flags.printing``
     - 1
     - Boolean
     - ``true`` if the printer is currently printing, ``false`` otherwise
   * - ``flags.sdReady``
     - 1
     - Boolean
     - ``true`` if the printer's SD card is available and initialized, ``false`` otherwise. This is redundant information
       to :ref:`the SD State <sec-api-printer-datamodel-sdstate>`.
   * - ``flags.error``
     - 1
     - Boolean
     - ``true`` if an unrecoverable error occurred, ``false`` otherwise
   * - ``flags.ready``
     - 1
     - Boolean
     - ``true`` if the printer is operational and no data is currently being streamed to SD, so ready to receive instructions
   * - ``flags.closedOrError``
     - 1
     - Boolean
     - ``true`` if the printer is disconnected (possibly due to an error), ``false`` otherwise

.. _sec-api-datamodel-printer-tempdata:

Temperature Data
----------------

.. list-table::
   :widths: 15 5 10 30
   :header-rows: 1

   * - Name
     - Multiplicity
     - Type
     - Description
   * - ``actual``
     - 1
     - Number
     - Current temperature
   * - ``target``
     - 1
     - Number
     - Target temperature, may be ``null`` if no target temperature is set.
   * - ``offset``
     - 0..1
     - Number
     - Currently configured temperature offset to apply, will be left out for historic temperature information.

.. _sec-api-datamodel-printer-temphistory:

Historic Temperature Data Point
-------------------------------

.. list-table::
   :widths: 15 5 10 30
   :header-rows: 1

   * - Name
     - Multiplicity
     - Type
     - Description
   * - ``time``
     - 1
     - Unix Timestamp
     - Timestamp of this data point
   * - ``tool{n}``
     - 0..*
     - :ref:`Temperature Data <sec-api-datamodel-printer-tempdata>`
     - Temperature stats for tool *n*. Enumeration starts at 0 for the first tool. Not included if querying only
       bed state.
   * - ``bed``
     - 0..*
     - :ref:`Temperature Data <sec-api-datamodel-printer-tempdata>`
     - Temperature stats for the printer's heated bed. Not included if querying only tool state.

.. _sec-api-datamodel-printer-tempoffset:

Temperature offset
------------------

.. list-table::
   :widths: 15 5 10 30
   :header-rows: 1

   * - Name
     - Multiplicity
     - Type
     - Description
   * - ``tool{n}``
     - 0..1
     - Number
     - Temperature offset for tool *n*. Enumeration starts at 0 for the first tool.
   * - ``bed``
     - 0..1
     - Number
     - Temperature offset for the printer's heated bed.

.. _sec-api-datamodel-jobs:

Job related
===========

.. _sec-api-datamodel-jobs-job:

Job information
---------------

.. list-table::
   :widths: 15 5 10 30
   :header-rows: 1

   * - Name
     - Multiplicity
     - Type
     - Description
   * - ``file``
     - 1
     - :ref:`File information (abridged) <sec-api-datamodel-files-file>`
     - The file that is the target of the current print job
   * - ``estimatedPrintTime``
     - 0..1
     - Integer
     - The estimated print time for the file, in seconds.
   * - ``lastPrintTime``
     - 0..1
     - Integer
     - The print time of the last print of the file, in seconds.
   * - ``filament``
     - 0..1
     - Object
     - Information regarding the estimated filament usage of the print job
   * - ``filament.length``
     - 0..1
     - Integer
     - Length of filament used, in mm
   * - ``filament.volume``
     - 0..1
     - Float
     - Volume of filament used, in cm³

.. _sec-api-datamodel-jobs-progress:

Progress information
--------------------

.. list-table::
   :widths: 15 5 10 30
   :header-rows: 1

   * - Name
     - Multiplicity
     - Type
     - Description
   * - ``completion``
     - 1
     - Float
     - Percentage of completion of the current print job
   * - ``filepos``
     - 1
     - Integer
     - Current position in the file being printed, in bytes from the beginning
   * - ``printTime``
     - 1
     - Integer
     - Time already spent printing, in seconds
   * - ``printTimeLeft``
     - 1
     - Integer
     - Estimate of time left to print, in seconds

.. _sec-api-datamodel-files:

File related
============

.. todo::

   Update to reflect enhanced data now available.

.. _sec-api-datamodel-files-file:

File information
----------------

.. list-table::
   :widths: 15 5 10 30
   :header-rows: 1

   * - Name
     - Multiplicity
     - Type
     - Description
   * - ``name``
     - 1
     - String
     - The name of the file
   * - ``type``
     - 1
     - String
     - Type of file. ``model`` or ``machinecode``. Or ``folder`` if it's a folder, in which case the ``children``
       node will be populated

Additional properties depend on ``type``. For a ``type`` value of ``folder``, see "Folders". For any other value
see "Files".

Folders
'''''''

.. list-table::
   :widths: 15 5 10 30
   :header-rows: 1

   * - Name
     - Multiplicity
     - Type
     - Description
   * - ``children``
     - 0..*
     - Array of :ref:`File information items <sec-api-datamodel-files-file>`
     - Contained children for entries of type ``folder``

Files
'''''

.. list-table::
   :widths: 15 5 10 30
   :header-rows: 1

   * - Name
     - Multiplicity
     - Type
     - Description
   * - ``hash``
     - 1
     - String
     - MD5 hash of the file
   * - ``size``
     - 0..1
     - Number
     - The size of the file in bytes. Only available for ``local`` files or ``sdcard`` files if the printer
       supports file sizes for sd card files.
   * - ``date``
     - 0..1
     - Unix timestamp
     - The timestamp when this file was uploaded. Only available for ``local`` files.
   * - ``origin``
     - 1
     - String, either ``local`` or ``sdcard``
     - The origin of the file, ``local`` when stored in OctoPrint's ``uploads`` folder, ``sdcard`` when stored on the
       printer's SD card (if available)
   * - ``refs``
     - 0..1
     - :ref:`sec-api-datamodel-files-ref`
     - References relevant to this file, left out in abridged version
   * - ``gcodeAnalysis``
     - 0..1
     - :ref:`GCODE analysis information <sec-api-datamodel-files-gcodeanalysis>`
     - Information from the analysis of the GCODE file, if available. Left out in abridged version.

.. _sec-api-datamodel-files-gcodeanalysis:

GCODE analysis information
--------------------------

.. list-table::
   :widths: 15 5 10 30
   :header-rows: 1

   * - Name
     - Multiplicity
     - Type
     - Description
   * - ``estimatedPrintTime``
     - 0..1
     - Integer
     - The estimated print time of the file, in seconds
   * - ``filament``
     - 0..1
     - Object
     - The estimated usage of filament
   * - ``filament.length``
     - 0..1
     - Integer
     - The length of filament used, in mm
   * - ``filament.volume``
     - 0..1
     - Float
     - The volume of filament used, in cm³

.. _sec-api-datamodel-files-ref:

References
----------

.. list-table::
   :widths: 15 5 10 30
   :header-rows: 1

   * - Name
     - Multiplicity
     - Type
     - Description
   * - ``resource``
     - 1
     - URL
     - The resource that represents the file (e.g. for issuing commands to or for deleting)
   * - ``download``
     - 0..1
     - URL
     - The download URL for the file
   * - ``model``
     - 0..1
     - URL
     - The model from which this file was generated (e.g. an STL, currently not used)

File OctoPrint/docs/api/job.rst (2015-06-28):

.. _sec-api-jobs:

**************
Job operations
**************

.. contents::

.. _sec-api-jobs-command:

Issue a job command
===================

.. http:post:: /api/job

   Job commands allow starting, pausing and cancelling print jobs. Available commands are:

   start
     Starts the print of the currently selected file. For selecting a file, see :ref:`Issue a file command <sec-api-fileops-filecommand>`.
     If a print job is already active, a :http:statuscode:`409` will be returned.

   restart
     Restart the print of the currently selected file from the beginning. There must be an active print job for this to work
     and the print job must currently be paused. If either is not the case, a :http:statuscode:`409` will be returned.

   pause
     Pauses/unpauses the current print job. If no print job is active (either paused or printing), a :http:statuscode:`409`
     will be returned.

   cancel
     Cancels the current print job.  If no print job is active (either paused or printing), a :http:statuscode:`409`
     will be returned.

   Upon success, a status code of :http:statuscode:`204` and an empty body is returned.

   **Example Start Request**

   .. sourcecode:: http

      POST /api/control/job HTTP/1.1
      Host: example.com
      Content-Type: application/json
      X-Api-Key: abcdef...

      {
        "command": "start"
      }

   .. sourcecode:: http

      HTTP/1.1 204 No Content

   **Example Restart Request**

   .. sourcecode:: http

      POST /api/control/job HTTP/1.1
      Host: example.com
      Content-Type: application/json
      X-Api-Key: abcdef...

      {
        "command": "restart"
      }

   .. sourcecode:: http

      HTTP/1.1 204 No Content

   **Example Pause Request**

   .. sourcecode:: http

      POST /api/control/job HTTP/1.1
      Host: example.com
      Content-Type: application/json
      X-Api-Key: abcdef...

      {
        "command": "pause"
      }

   .. sourcecode:: http

      HTTP/1.1 204 No Content

   **Example Cancel Request**

   .. sourcecode:: http

      POST /api/control/job HTTP/1.1
      Host: example.com
      Content-Type: application/json
      X-Api-Key: abcdef...

      {
        "command": "cancel"
      }

   .. sourcecode:: http

      HTTP/1.1 204 No Content

   :json string command: The command to issue, either ``start``, ``restart``, ``pause`` or ``cancel``
   :statuscode 204:      No error
   :statuscode 409:      If the printer is not operational or the current print job state does not match the preconditions
                         for the command.

.. _sec-api-job-information:

Retrieve information about the current job
==========================================

.. http:get:: /api/job

   Retrieve information about the current job (if there is one).

   Returns a :http:statuscode:`200` with a :ref:`sec-api-job-datamodel-response` in the body.

   **Example**

   .. sourcecode:: http

      GET /api/job HTTP/1.1
      Host: example.com
      X-Api-Key: abcdef...

   .. sourcecode:: http

      HTTP/1.1 200 OK
      Content-Type: application/json

      {
        "job": {
          "file": {
            "name": "whistle_v2.gcode",
            "origin": "local",
            "size": 1468987,
            "date": 1378847754
          },
          "estimatedPrintTime": 8811,
          "filament": {
            "length": 810,
            "volume": 5.36
          }
        },
        "progress": {
          "completion": 0.2298468264184775,
          "filepos": 337942,
          "printTime": 276,
          "printTimeLeft": 912
        }
      }

   :statuscode 200: No error

.. _sec-api-job-datamodel:

Datamodel
=========

.. _sec-api-job-datamodel-response:

Job information response
------------------------

.. list-table::
   :widths: 15 5 10 30
   :header-rows: 1

   * - Name
     - Multiplicity
     - Type
     - Description
   * - ``job``
     - 1
     - :ref:`sec-api-datamodel-jobs-job`
     - Information regarding the target of the current print job
   * - ``progress``
     - 1
     - :ref:`sec-api-datamodel-jobs-progress`
     - Information regarding the progress of the current print job

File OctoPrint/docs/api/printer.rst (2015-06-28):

.. _sec-api-printer:

******************
Printer operations
******************

.. warning::

   This part of the API is still heavily in development, especially anything that has to do with temperature control.
   If you happen to want to develop against it, you should drop me an email to make sure I can give you a heads-up when
   something changes.

.. contents::

Printer control is mostly achieved through the use of commands, issued to resources reflecting components of the
printer. OctoPrint currently knows the following components:

Print head
  Print head commands allow jogging and homing the print head in all three axes. Querying the resource is currently
  not supported.
  See :ref:`sec-api-printer-printheadcommand`.
Tool
  Tool commands allow setting the temperature and temperature offsets for the printer's hotends/tools. Querying the
  corresponding resource returns temperature information including an optional history.
  See :ref:`sec-api-printer-toolcommand`.
Bed
  Bed commands allow setting the temperature and temperature offset for the printer's heated bed. Querying the
  corresponding resource returns temperature information including an optional history.
  See :ref:`sec-api-printer-bedcommand`.
SD card
  SD commands allow initialization, refresh and release of the printer's SD card (if available). Querying the
  corresponding resource returns the current SD card state.
  See :ref:`sec-api-printer-sdcommand`.

Besides that, OctoPrint also provides a :ref:`full state report of the printer <sec-api-printer-state>`.

.. _sec-api-printer-state:

Retrieve the current printer state
==================================

.. http:get:: /api/printer

   Retrieves the current state of the printer. Returned information includes:

   * temperature information (see also :ref:`Retrieve the current tool state <sec-api-printer-toolstate>` and
     :ref:`Retrieve the current bed state <sec-api-printer-bedstate>`)
   * sd state (if available, see also :ref:`Retrieve the current SD state <sec-api-printer-sdstate>`)
   * general printer state

   Temperature information can also be made to include the printer's temperature history by supplying the ``history``
   query parameter. The amount of data points to return here can be limited using the ``limit`` query parameter.

   Clients can specific a list of attributes to not return in the response (e.g. if they don't need it) via the
   ``exclude`` query parameter.

   Returns a :http:statuscode:`200` with a :ref:`Full State Response <sec-api-printer-datamodel-fullstate>` in the
   body upon success.

   **Example 1**

   Include temperature history data, but limit it to two entries.

   .. sourcecode:: http

      GET /api/printer?history=true&limit=2 HTTP/1.1
      Host: example.com
      X-Api-Key: abcdef...

   .. sourcecode:: http

      HTTP/1.1 200 OK
      Content-Type: application/json

      {
        "temperature": {
          "tool0": {
            "actual": 214.8821,
            "target": 220.0,
            "offset": 0
          },
          "tool1": {
            "actual": 25.3,
            "target": null,
            "offset": 0
          },
          "bed": {
            "actual": 50.221,
            "target": 70.0,
            "offset": 5
          },
          "history": [
            {
              "time": 1395651928,
              "tool0": {
                "actual": 214.8821,
                "target": 220.0
              },
              "tool1": {
                "actual": 25.3,
                "target": null
              },
              "bed": {
                "actual": 50.221,
                "target": 70.0
              }
            },
            {
              "time": 1395651926,
              "tool0": {
                "actual": 212.32,
                "target": 220.0
              },
              "tool1": {
                "actual": 25.1,
                "target": null
              },
              "bed": {
                "actual": 49.1123,
                "target": 70.0
              }
            }
          ]
        },
        "sd": {
          "ready": true
        },
        "state": {
          "text": "Operational",
          "flags": {
            "operational": true,
            "paused": false,
            "printing": false,
            "sdReady": true,
            "error": false,
            "ready": true,
            "closedOrError": false
          }
        }
      }

   **Example 2**

   Exclude temperature and sd data.

   .. sourcecode:: http

      GET /api/printer?exclude=temperature,sd HTTP/1.1
      Host: example.com
      X-Api-Key: abcdef...

   .. sourcecode:: http

      HTTP/1.1 200 OK
      Content-Type: application/json

      {
        "state": {
          "text": "Operational",
          "flags": {
            "operational": true,
            "paused": false,
            "printing": false,
            "sdReady": true,
            "error": false,
            "ready": true,
            "closedOrError": false
          }
        }
      }

   :query exclude:  An optional comma-separated list of fields to exclude from the response (e.g. if not needed by
                    the client). Valid values to supply here are ``temperature``, ``sd`` and ``state``.
   :query history:  If set to ``true`` (or: ``yes``, ``y``, ``1``), history information will be included in the response
                    too. If no ``limit`` parameter is given, all available temperature history data will be returned.
   :query limit:    If set to an integer (``n``), only the last ``n`` data points from the printer's temperature history
                    will be returned. Will be ignored if ``history`` is not enabled.
   :statuscode 200: No error
   :statuscode 409: If the printer is not operational.

.. _sec-api-printer-printheadcommand:

Issue a print head command
==========================

.. http:post:: /api/printer/printhead

   Print head commands allow jogging and homing the print head in all three axes. Available commands are:

   jog
     Jogs the print head (relatively) by a defined amount in one or more axes. Additional parameters are:

     * ``x``: Optional. Amount to jog print head on x axis, must be a valid number corresponding to the distance to travel in mm.
     * ``y``: Optional. Amount to jog print head on y axis, must be a valid number corresponding to the distance to travel in mm.
     * ``z``: Optional. Amount to jog print head on z axis, must be a valid number corresponding to the distance to travel in mm.

   home
     Homes the print head in all of the given axes. Additional parameters are:

     * ``axes``: A list of axes which to home, valid values are one or more of ``x``, ``y``, ``z``.

   feedrate
     Changes the feedrate factor to apply to the movement's of the axes.

     * ``factor``: The new factor, percentage as integer or float (percentage divided by 100) between 50 and 200%.

   All of these commands except ``feedrate`` may only be sent if the printer is currently operational and not printing.
   Otherwise a :http:statuscode:`409` is returned.

   Upon success, a status code of :http:statuscode:`204` and an empty body is returned.

   **Example Jog Request**

   Jog the print head by 10mm in X, -5mm in Y and 0.02mm in Z.

   .. sourcecode:: http

      POST /api/printer/printhead HTTP/1.1
      Host: example.com
      Content-Type: application/json
      X-Api-Key: abcdef...

      {
        "command": "jog",
        "x": 10,
        "y": -5,
        "z": 0.02
      }

   .. sourcecode:: http

      HTTP/1.1 204 No Content

   **Example Home Request**

   Home the X and Y axes.

   .. sourcecode:: http

      POST /api/printer/printhead HTTP/1.1
      Host: example.com
      Content-Type: application/json
      X-Api-Key: abcdef...

      {
        "command": "home",
        "axes": ["x", "y"]
      }

   .. sourcecode:: http

      HTTP/1.1 204 No Content

   **Example feed rate request**

   Set the feed rate factor to 105%.

   .. sourcecode:: http

      POST /api/printer/printhead HTTP/1.1
      Host: example.com
      Content-Type: application/json
      X-Api-Key: abcdef...

      {
        "command": "feedrate",
        "factor": 105
      }

   .. sourcecode:: http

      HTTP/1.1 204 No Content

   :json string command: The command to issue, either ``jog`` or ``home``.
   :json number x:       ``jog`` command: The amount to travel on the X axis in mm.
   :json number y:       ``jog`` command: The amount to travel on the Y axis in mm.
   :json number z:       ``jog`` command: The amount to travel on the Z axis in mm.
   :json array axes:     ``home`` command: The axes which to home, valid values are one or more of ``x``, ``y`` and ``z``.
   :json number factor:  ``feedrate`` command: The factor to apply to the feed rate, percentage between 50 and 200% as integer or float.
   :statuscode 204: No error
   :statuscode 400: Invalid axis specified, invalid value for travel amount for a jog command or factor for feed rate or otherwise invalid
                    request.
   :statuscode 409: If the printer is not operational or currently printing.

.. _sec-api-printer-toolcommand:

Issue a tool command
====================

.. http:post:: /api/printer/tool

   Tool commands allow setting the temperature and temperature offsets for the printer's tools (hotends), selecting
   the current tool and extruding/retracting from the currently selected tool. Available commands are:

   target
     Sets the given target temperature on the printer's tools. Additional parameters:

     * ``targets``: Target temperature(s) to set, properties must match the format ``tool{n}`` with ``n`` being the
       tool's index starting with 0.

   offset
     Sets the given temperature offset on the printer's tools. Additional parameters:

     * ``offsets``: Offset(s) to set, properties must match the format ``tool{n}`` with ``n`` being the tool's index
       starting with 0.

   select
     Selects the printer's current tool. Additional parameters:

     * ``tool``: Tool to select, format ``tool{n}`` with ``n`` being the tool's index starting with 0.

   extrude
     Extrudes the given amount of filament from the currently selected tool. Additional parameters:

     * ``amount``: The amount of filament to extrude in mm. May be negative to retract.

   flowrate
     Changes the flow rate factor to apply to extrusion of the tool.

     * ``factor``: The new factor, percentage as integer or float (percentage divided by 100) between 75 and 125%.

   All of these commands may only be sent if the printer is currently operational and -- in case of ``select`` and
   ``extrude`` -- not printing. Otherwise a :http:statuscode:`409` is returned.

   Upon success, a status code of :http:statuscode:`204` and an empty body is returned.

   **Example Target Temperature Request**

   Set the target temperature for the printer's first hotend to 220°C and the printer's second extruder to 205°C.

   .. sourcecode:: http

      POST /api/printer/tool HTTP/1.1
      Host: example.com
      Content-Type: application/json
      X-Api-Key: abcdef...

      {
        "command": "target",
        "targets": {
          "tool0": 220,
          "tool1": 205
        }
      }

   .. sourcecode:: http

      HTTP/1.1 204 No Content

   **Example Offset Temperature Request**

   Set the offset for temperatures on ``tool0`` to +10°C and on ``tool1`` to -5°C.

   .. sourcecode:: http

      POST /api/printer/tool HTTP/1.1
      Host: example.com
      Content-Type: application/json
      X-Api-Key: abcdef...

      {
        "command": "offset",
        "offsets": {
          "tool0": 10,
          "tool1": -5
        }
      }

   .. sourcecode:: http

      HTTP/1.1 204 No Content

   **Example Tool Select Request**

   Select the second hotend of the printer for any following ``extrude`` commands.

   .. sourcecode:: http

      POST /api/printer/tool HTTP/1.1
      Host: example.com
      Content-Type: application/json
      X-Api-Key: abcdef...

      {
        "command": "select",
        "tool": "tool1"
      }

   .. sourcecode:: http

      HTTP/1.1 204 No Content

   **Example Extrude Request**

   Extrude 5mm on the currently selected tool.

   .. sourcecode:: http

      POST /api/printer/tool HTTP/1.1
      Host: example.com
      Content-Type: application/json
      X-Api-Key: abcdef...

      {
        "command": "extrude",
        "amount": 5
      }

   .. sourcecode:: http

      HTTP/1.1 204 No Content

   **Example Retract Request**

   Retract 3mm of filament on the currently selected tool.

   .. sourcecode:: http

      POST /api/printer/tool HTTP/1.1
      Host: example.com
      Content-Type: application/json
      X-Api-Key: abcdef...

      {
        "command": "extrude",
        "amount": -3
      }

   .. sourcecode:: http

      HTTP/1.1 204 No Content

   **Example flow rate request**

   Set the flow rate factor to 95%.

   .. sourcecode:: http

      POST /api/printer/tool HTTP/1.1
      Host: example.com
      Content-Type: application/json
      X-Api-Key: abcdef...

      {
        "command": "flowrate",
        "factor": 95
      }

   .. sourcecode:: http

      HTTP/1.1 204 No Content

   :json string command: The command to issue, either ``target``, ``offset``, ``select`` or ``extrude``.
   :json object targets: ``target`` command: The target temperatures to set. Valid properties have to match the format ``tool{n}``.
   :json object offsets: ``offset`` command: The offset temperature to set. Valid properties have to match the format ``tool{n}``.
   :json object tool:    ``select`` command: The tool to select, value has to match the format ``tool{n}``.
   :json object amount:  ``extrude`` command: The amount of filament to extrude from the currently selected tool.
   :json number factor:  ``flowrate`` command: The factor to apply to the flow rate, percentage between 75 and 125% as integer or float.
   :statuscode 204: No error
   :statuscode 400: If ``targets`` or ``offsets`` contains a property or ``tool`` contains a value not matching the format
                    ``tool{n}``, the target/offset temperature, extrusion amount or flow rate factor is not a valid number or outside of
                    the supported range, or if the request is otherwise invalid.
   :statuscode 409: If the printer is not operational or -- in case of ``select`` or ``extrude`` -- currently printing.

.. _sec-api-printer-toolstate:

Retrieve the current tool state
===============================

.. http:get:: /api/printer/tool

   Retrieves the current temperature data (actual, target and offset) plus optionally a (limited) history (actual, target,
   timestamp) for all of the printer's available tools.

   It's also possible to retrieve the temperature history by supplying the ``history`` query parameter set to ``true``. The
   amount of returned history data points can be limited using the ``limit`` query parameter.

   Returns a :http:statuscode:`200` with a Temperature Response in the body upon success.

   .. note::
      If you want both tool and bed temperature information at the same time, take a look at
      :ref:`Retrieve the current printer state <sec-api-printer-state>`.

   **Example**

   Query the tool temperature data and also include the temperature history but limit it to two entries.

   .. sourcecode:: http

      GET /api/printer/tool?history=true&limit=2 HTTP/1.1
      Host: example.com
      X-Api-Key: abcdef...

   .. sourcecode:: http

      HTTP/1.1 200 OK
      Content-Type: application/json

      {
        "tool0": {
          "actual": 214.8821,
          "target": 220.0,
          "offset": 0
        },
        "tool1": {
          "actual": 25.3,
          "target": null,
          "offset": 0
        },
        "history": [
          {
            "time": 1395651928,
            "tool0": {
              "actual": 214.8821,
              "target": 220.0
            },
            "tool1": {
              "actual": 25.3,
              "target": null
            }
          },
          {
            "time": 1395651926,
            "tool0": {
              "actual": 212.32,
              "target": 220.0
            },
            "tool1": {
              "actual": 25.1
            }
          }
        ]
      }

   :query history:  If set to ``true`` (or: ``yes``, ``y``, ``1``), history information will be included in the response
                    too. If no ``limit`` parameter is given, all available temperature history data will be returned.
   :query limit:    If set to an integer (``n``), only the last ``n`` data points from the printer's temperature history
                    will be returned. Will be ignored if ``history`` is not enabled.
   :statuscode 200: No error
   :statuscode 409: If the printer is not operational.

.. _sec-api-printer-bedcommand:

Issue a bed command
===================

.. http:post:: /api/printer/bed

   Bed commands allow setting the temperature and temperature offsets for the printer's heated bed. Available commands
   are:

   target
     Sets the given target temperature on the printer's tools. Additional parameters:

     * ``target``: Target temperature to set.

   offset
     Sets the given temperature offset on the printer's tools. Additional parameters:

     * ``offset``: Offset to set.

   All of these commands may only be sent if the printer is currently operational. Otherwise a :http:statuscode:`409`
   is returned.

   Upon success, a status code of :http:statuscode:`204` and an empty body is returned.

   **Example Target Temperature Request**

   Set the target temperature for the printer's heated bed to 75°C.

   .. sourcecode:: http

      POST /api/printer/bed HTTP/1.1
      Host: example.com
      Content-Type: application/json
      X-Api-Key: abcdef...

      {
        "command": "target",
        "target": 75
      }

   .. sourcecode:: http

      HTTP/1.1 204 No Content

   **Example Offset Temperature Request**

   Set the temperature offset for the heated bed to -5°C.

   .. sourcecode:: http

      POST /api/printer/bed HTTP/1.1
      Host: example.com
      Content-Type: application/json
      X-Api-Key: abcdef...

      {
        "command": "offset",
        "offset": -5
      }

   .. sourcecode:: http

      HTTP/1.1 204 No Content

   :json string command: The command to issue, either ``target`` or ``offset``.
   :json object target: ``target`` command: The target temperature to set.
   :json object offset: ``offset`` command: The offset temperature to set.
   :statuscode 204: No error
   :statuscode 400: If ``target`` or ``offset`` is not a valid number or outside of the supported range, or if the
                    request is otherwise invalid.
   :statuscode 409: If the printer is not operational.

.. _sec-api-printer-bedstate:

Retrieve the current bed state
==============================

.. http:get:: /api/printer/bed

   Retrieves the current temperature data (actual, target and offset) plus optionally a (limited) history (actual, target,
   timestamp) for the printer's heated bed.

   It's also possible to retrieve the temperature history by supplying the ``history`` query parameter set to ``true``. The
   amount of returned history data points can be limited using the ``limit`` query parameter.

   Returns a :http:statuscode:`200` with a Temperature Response in the body upon success.

   .. note::
      If you want both tool and bed temperature information at the same time, take a look at
      :ref:`Retrieve the current printer state <sec-api-printer-state>`.

   **Example**

   Query the bed temperature data and also include the temperature history but limit it to two entries.

   .. sourcecode:: http

      GET /api/printer/bed?history=true&limit=2 HTTP/1.1
      Host: example.com
      X-Api-Key: abcdef...

   .. sourcecode:: http

      HTTP/1.1 200 OK
      Content-Type: application/json

      {
        "bed": {
          "actual": 50.221,
          "target": 70.0,
          "offset": 5
        },
        "history": [
          {
            "time": 1395651928,
            "bed": {
              "actual": 50.221,
              "target": 70.0
            }
          },
          {
            "time": 1395651926,
            "bed": {
              "actual": 49.1123,
              "target": 70.0
            }
          }
        ]
      }

   :query history:  If set to ``true`` (or: ``yes``, ``y``, ``1``), history information will be included in the response
                    too. If no ``limit`` parameter is given, all available temperature history data will be returned.
   :query limit:    If set to an integer (``n``), only the last ``n`` data points from the printer's temperature history
                    will be returned. Will be ignored if ``history`` is not enabled.
   :statuscode 200: No error
   :statuscode 409: If the printer is not operational.

.. _sec-api-printer-sdcommand:

Issue an SD command
===================

.. http:post:: /api/printer/sd

   SD commands allow initialization, refresh and release of the printer's SD card (if available).

   Available commands are:

   init
     Initializes the printer's SD card, making it available for use. This also includes an initial retrieval of the
     list of files currently stored on the SD card, so after issueing that command a :ref:`retrieval of the files
     on SD card <sec-api-fileops-retrievelocation>` will return a successful result.

     .. note::
        If OctoPrint detects the availability of a SD card on the printer during connection, it will automatically attempt
        to initialize it.

   refresh
     Refreshes the list of files stored on the printer's SD card. Will return a :http:statuscode:`409` if the card
     has not been initialized yet (see the ``init`` command and :ref:`SD state <sec-api-printer-sdstate>`).

   release
     Releases the SD card from the printer. The reverse operation to ``init``. After issuing this command, the SD
     card won't be available anymore, hence and operations targeting files stored on it will fail. Will return a :http:statuscode:`409`
     if the card has not been initialized yet (see the ``init`` command and :ref:`SD state <sec-api-printer-sdstate>`).

   Upon success, a status code of :http:statuscode:`204` and an empty body is returned.

   **Example Init Request**

   Initialize the SD card.

   .. sourcecode:: http

      POST /api/printer/sd HTTP/1.1
      Host: example.com
      Content-Type: application/json
      X-Api-Key: abcdef...

      {
        "command": "init"
      }

   .. sourcecode:: http

      HTTP/1.1 204 No Content

   **Example Refresh Request**

   Refresh the file list of the SD card

   .. sourcecode:: http

      POST /api/printer/sd HTTP/1.1
      Host: example.com
      Content-Type: application/json
      X-Api-Key: abcdef...

      {
        "command": "refresh"
      }

   .. sourcecode:: http

      HTTP/1.1 204 No Content

   **Example Release Request**

   Release the SD card

   .. sourcecode:: http

      POST /api/printer/sd HTTP/1.1
      Host: example.com
      Content-Type: application/json
      X-Api-Key: abcdef...

      {
        "command": "release"
      }

   .. sourcecode:: http

      HTTP/1.1 204 No Content

   :json string command: The command to issue, either ``init``, ``refresh`` or ``release``.
   :statuscode 204:      No error
   :statuscode 409:      If a ``refresh`` or ``release`` command is issued but the SD card has not been initialized (e.g.
                         via ``init``.

.. _sec-api-printer-sdstate:

Retrieve the current SD state
=============================

.. http:get:: /api/printer/sd

   Retrieves the current state of the printer's SD card. For this request no authentication is needed.

   If SD support has been disabled in OctoPrint's settings, a :http:statuscode:`404` is returned.

   Returns a :http:statuscode:`200` with an :ref:`SD State Response <sec-api-printer-datamodel-sdstate>` in the body
   upon success.

   **Example**

   Read the current state of the SD card.

   .. sourcecode:: http

      GET /api/printer/sd HTTP/1.1
      Host: example.com
      X-Api-Key: abcdef...

   .. sourcecode:: http

      HTTP/1.1 200 OK
      Content-Type: application/json

      {
        "ready": true
      }

   :statuscode 200: No error
   :statuscode 404: If SD support has been disabled in OctoPrint's config.

.. _sec-api-printer-arbcommand:

Send an arbitrary command to the printer
========================================

.. http:post:: /api/printer/command

   Sends any command to the printer via the serial interface. Should be used with some care as some commands can interfere with
   or even stop a running print job.

   Expects a :ref:`Arbitrary Command Request <sec-api-printer-datamodel-arbcommand>` as the request's body.

   If successful returns a :http:statuscode:`204` and an empty body.

   **Example for sending a single command**

   .. sourcecode:: http

      POST /api/printer/command HTTP/1.1
      Host: example.com
      Content-Type: application/json
      X-Api-Key: abcdef...

      {
        "command": "M106"
      }

   .. sourcecode:: http

      HTTP/1.1 204 No Content

   **Example for sending multiple commands**

   .. sourcecode:: http

      POST /api/printer/command HTTP/1.1
      Host: example.com
      Content-Type: application/json
      X-Api-Key: abcdef...

      {
        "commands": [
          "M18",
          "M106 S0"
        ]
      }

   .. sourcecode:: http

      HTTP/1.1 204 No Content
   
   :json string command:  Single command to send to the printer, mutually exclusive with ``commands``.
   :json string commands: List of commands to send to the printer, mutually exclusive with ``command``.
   :statuscode 204:       No error

.. _sec-api-printer-datamodel:

Datamodel
=========

.. _sec-api-printer-datamodel-fullstate:

Full State Response
-------------------

.. list-table::
   :widths: 15 5 10 30
   :header-rows: 1

   * - Name
     - Multiplicity
     - Type
     - Description
   * - ``temperature``
     - 0..1
     - :ref:`Temperature State <sec-api-printer-datamodel-temps>`
     - The printer's temperature state data
   * - ``sd``
     - 0..1
     - :ref:`SD State <sec-api-printer-datamodel-sdstate>`
     - The printer's sd state data
   * - ``state``
     - 0..1
     - :ref:`Printer State <sec-api-datamodel-printer-state>`
     - The printer's general state

.. _sec-api-printer-datamodel-temps:

Temperature State
-----------------

.. list-table::
   :widths: 15 5 10 30
   :header-rows: 1

   * - Name
     - Multiplicity
     - Type
     - Description
   * - ``tool{n}``
     - 0..*
     - :ref:`Temperature Data <sec-api-datamodel-printer-tempdata>`
     - Current temperature stats for tool *n*. Enumeration starts at 0 for the first tool. Not included if querying
       only bed state.
   * - ``bed``
     - 0..1
     - :ref:`Temperature Data <sec-api-datamodel-printer-tempdata>`
     - Current temperature stats for the printer's heated bed. Not included if querying only tool state.
   * - ``history``
     - 0..1
     - List of :ref:`Historic Temperature Datapoint <sec-api-datamodel-printer-temphistory>`
     - Temperature history

.. _sec-api-printer-datamodel-sdstate:

SD State
--------

.. list-table::
   :widths: 15 5 10 30
   :header-rows: 1

   * - Name
     - Multiplicity
     - Type
     - Description
   * - ``ready``
     - 1
     - Boolean
     - Whether the SD card has been initialized (``true``) or not (``false``).

.. _sec-api-printer-datamodel-arbcommand:

Arbitrary Command Request
-------------------------

.. list-table::
   :widths: 15 5 10 30
   :header-rows: 1

   * - Name
     - Multiplicity
     - Type
     - Description
   * - ``command``
     - 0..1
     - String
     - Single command to send to the printer, mutually exclusive with ``commands`` and ``script``.
   * - ``commands``
     - 0..*
     - Array of String
     - Multiple commands to send to the printer (in the given order), mutually exclusive with ``command`` and ``script``.
   * - ``script``
     - 0..*
     - String
     - Name of the GCODE script template to send to the printer, mutually exclusive with ``command`` and ``commands``.
   * - ``parameters``
     - 0..1
     - Map of key value pairs
     - Key value pairs of parameters to replace in sent commands/provide to the script renderer
   * - ``context``
     - 0..1
     - Map of key value pairs
     - (only if ``script`` is set) additional template variables to provide to the script renderer

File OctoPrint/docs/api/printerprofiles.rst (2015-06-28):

.. _sec-api-printerprofiles:

**************************
Printer profile operations
**************************

.. contents::

OctoPrint allows the management of Printer profiles that define a printer's physical properties (such as print volume,
whether a heated bed is available, maximum speeds on its axes etc). The data stored within these profiles is used
for both slicing and gcode visualization.

.. _sec-api-printerprofiles-retrieve:

Retrieve all printer profiles
=============================

.. http:get:: /api/printerprofiles

.. _sec-api-printerprofiles-add:

Add a new printer profile
=========================

.. http:post:: /api/printerprofiles

.. _sec-api-printerporfiles-update:

Update an existing printer profile
==================================

.. http:patch:: /api/printerprofiles/(string:profile)

.. _sec-api-printerprofiles-delete:

Remove an existing printer profile
==================================

.. http:delete:: /api/printerprofiles/(string:profile)

.. _sec-api-printerprofiles-datamodel:

Datamodel
=========

.. _sec-api-printerprofiles-datamodel-profilelist:

Profile list
------------

.. list-table::
   :widths: 15 5 10 30
   :header-rows: 1

   * - Name
     - Multiplicity
     - Type
     - Description
   * - ``profiles``
     - 1
     - Object
     - Collection of all printer profiles available in the system
   * - ``profiles.<profile id>``
     - 0..1
     - :ref:`Profile <sec-api-slicing-datamodel-profile>`
     - Information about a profile stored in the system.

.. _sec-api-printerprofiles-datamodel-update:

Add or update request
---------------------

.. list-table::
   :widths: 15 5 10 30
   :header-rows: 1

   * - Name
     - Multiplicity
     - Type
     - Description
   * - ``profiles``
     - 1
     - :ref:`Profile <sec-api-slicing-datamodel-profile>`
     - Information about the profile being added/updated. For adding new profiles, all fields must be populated. For updating
       and existing profile, only the values to be overwritten need to be supplied.

.. _sec-api-printerprofiles-datamodel-profile:

Profile
-------

.. list-table::
   :widths: 15 5 10 30
   :header-rows: 1

   * - Name
     - Multiplicity
     - Type
     - Description
   * - ``id``
     - 0..1
     - ``string``
     - Identifier of the profile. Will always be
       returned in responses but can be left out of save/update requests.
   * - ``name``
     - 0..1
     - ``string``
     - Display name of the profile. Will always be
       returned in responses but can be left out of save/update requests.
   * - ``color``
     - 0..1
     - ``string``
     - The color to associate with this profile (used in the UI's title bar). Valid values are "default", "red", "orange",
       "yellow", "green", "blue", "black". Will always be
       returned in responses but can be left out of save/update requests.
   * - ``model``
     - 0..1
     - ``string``
     - Printer model of the profile. Will always be
       returned in responses but can be left out of save/update requests.
   * - ``default``
     - 0..1
     - ``boolean``
     - Whether this is the default profile to be used with new connections (``true``) or not (``false``). Will always be
       returned in responses but can be left out of save/update requests.
   * - ``current``
     - 0..1
     - ``boolean``
     - Whether this is the profile currently active. Will always be returned in responses but ignored in save/update
       requests.
   * - ``resource``
     - 0..1
     - ``URL``
     - Resource URL of the profile, will always be returned in responses but can be left out of save/update requests.
   * - ``volume``
     - 0..1
     - Object
     - The print volume, will always be returned in responses but can be left out of save/update requests.
   * - ``volume.formFactor``
     - 0..1
     - ``string``
     - The form factor of the printer's bed, valid values are "rectangular" and "circular"
   * - ``volume.width``
     - 0..1
     - ``float``
     - The width of the print volume
   * - ``volume.depth``
     - 0..1
     - ``float``
     - The depth of the print volume
   * - ``volume.height``
     - 0..1
     - ``float``
     - The height of the print volume
   * - ``heatedBed``
     - 0..1
     - ``boolean``
     - Whether the printer has a heated bed (``true``) or not (``false``)
   * - ``axes``
     - 0..1
     - Object
     - Description of the printer's axes properties, one entry each for ``x``, ``y``, ``z`` and ``e`` holding maxium speed
       and whether this axis is inverted or not.
   * - ``axes.{axis}.speed``
     - 0..1
     - ``int``
     - Maximum speed of the axis in mm/s.
   * - ``axes.{axis}.inverted``
     - 0..1
     - ``boolean``
     - Whether the axis is inverted or not.
   * - ``extruder``
     - 0..1
     - Object
     - Information about the printer's extruders
   * - ``extruder.nozzleDiameter``
     - 0..1
     - ``float``
     - The diameter of the printer's nozzle(s) in mm.
   * - ``extruder.count``
     - 0..1
     - ``int``
     - Count of extruders on the printer (defaults to 1)
   * - ``extruder.offsets``
     - 0..1
     - Array of ``float`` tuples
     - Tuple of (x, y) values describing the offsets of the other extruders relative to the first extruder. E.g. for a
       printer with two extruders, if the second extruder is offset by 20mm in the X and 25mm in the Y direction, this
       array will read ``[ [0.0, 0.0], [20.0, 25.0] ]``

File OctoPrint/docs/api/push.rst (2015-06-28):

.. _sec-api-push:

************
Push updates
************

.. warning::

   The interface documented here is the status quo that might be changed while the interfaces are streamlined for
   a more general consumption. If you happen to want to develop against it, you should drop me an email to make sure I can give you a heads-up when
   something changes.

.. contents::

To enable real time information exchange between client and server, OctoPrint uses 
`SockJS <https://github.com/sockjs/sockjs-protocol>`_ to push
status updates, temperature changes etc to connected web interface instances.

Each pushed message consists of a simple JSON object that follows this basic structure:

.. sourcecode:: javascript

   {
     "<type>": <payload>
   }

``type`` indicates the type of message being pushed to the client, the attached ``payload`` is message specific. The
following message types are currently available for usage by 3rd party clients:

  * ``current``: Rate limited general state update, payload contains information about the printer's state, job progress,
    accumulated temperature points and log lines since last update. OctoPrint will send these updates when new information
    is available, but not more often than twice per second in order to not flood the client with messages (e.g.
    during printing). See :ref:`the payload data model <sec-api-push-datamodel-currentandhistory>`.
  * ``history``: Current state, temperature and log history, sent upon initial connect to get the client up to date. Same
    payload data model as ``current``, see :ref:`below <sec-api-push-datamodel-currentandhistory>`.
  * ``event``: Events triggered within OctoPrint, such as e.g. ``PrintFailed`` or ``MovieRenderDone``. Payload is the event
    type and payload, see :ref:`below <sec-api-push-datamodel-event>`. Sent when an event is triggered internally.
  * ``slicingProgress``: Progress updates from an active slicing background job, payload contains information about the
    model being sliced, the target file, the slicer being used and the progress as a percentage.
    See :ref:`the payload data model <sec-api-push-datamodel-slicingprogress>`.

Clients must ignore any unknown messages.

The data model of the attached payloads is described further below.

.. _sec-api-push-datamodel:

Datamodel
=========

.. _sec-api-push-datamodel-currentandhistory:

``current`` and ``history`` payload
-----------------------------------

.. list-table::
   :widths: 15 5 10 30
   :header-rows: 1

   * - Name
     - Multiplicity
     - Type
     - Description
   * - ``state``
     - 1
     - :ref:`State information <sec-api-datamodel-printer-state>`
     - Information about the current machine state
   * - ``job``
     - 1
     - :ref:`Job information <sec-api-datamodel-jobs-job>`
     - Information about the currently active print job
   * - ``progress``
     - 1
     - :ref:`Progress information <sec-api-datamodel-jobs-progress>`
     - Information about the current print/streaming progress
   * - ``currentZ``
     - 1
     - Float
     - Current height of the Z-Axis (= current height of model) during printing from a local file
   * - ``offsets``
     - 0..1
     - :ref:`Temperature offsets <sec-api-datamodel-printer-tempoffset>`
     - Currently configured temperature offsets
   * - ``temps``
     - 0..*
     - List of :ref:`Temperature Data Points <sec-api-datamodel-printer-temphistory>`
     - Temperature data points for plotting
   * - ``logs``
     - 0..*
     - List of String
     - Lines for the serial communication log (send/receive)
   * - ``messages``
     - 0..*
     - List of String
     - Lines for the serial communication log (special messages)

.. _sec-api-push-datamodel-event:

``event`` payload
-----------------

.. list-table::
   :widths: 15 5 10 30
   :header-rows: 1

   * - Name
     - Multiplicity
     - Type
     - Description
   * - ``type``
     - 1
     - String
     - Name of the event
   * - ``payload``
     - 1
     - Object
     - Payload associated with the event

.. _sec-api-push-datamodel-slicingprogress:

``slicingProgress`` payload
---------------------------

.. list-table::
   :widths: 15 5 10 30
   :header-rows: 1

   * - Name
     - Multiplicity
     - Type
     - Description
   * - ``slicer``
     - 1
     - String
     - Name of the slicer used
   * - ``source_location``
     - 1
     - String
     - Location of the source file being sliced, at the moment either ``local`` or ``sdcard``
   * - ``source_path``
     - 1
     - String
     - Path of the source file being sliced (e.g. an STL file)
   * - ``dest_location``
     - 1
     - String
     - Location of the destination file being created, at the moment either ``local`` or ``sdcard``
   * - ``dest_path``
     - 1
     - String
     - Path of the destination file being sliced (e.g. a GCODE file)
   * - ``progress``
     - 1
     - Number (Float)
     - Percentage of slicing job already completed

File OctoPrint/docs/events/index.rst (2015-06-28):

.. _sec-events:

######
Events
######

.. contents::

.. note::

   With release of OctoPrint 1.1.0, the payload data has been harmonized, it is now a key-value-map for all events.
   Additionally, the format of the placeholders in both system command and gcode command triggers has been changed to
   accommodate for this new format. Last but not least, the way of specifying event hooks has changed, OctoPrint no longer
   separates hooks into two sections (gcodeCommandTrigger and systemCommandTrigger) but instead event hooks are now typed
   to indicate what to do with the command contained.

.. _sec-events-configuration:

Configuration
=============

Event hooks are configured via OctoPrint's configuration file ``config.yaml``. There they are contained in a
``subscriptions`` list located directly under the ``events`` node. The ``command`` node accepts either a single string
or a list of strings so that multiple commands can be executed in one go. Each hook carries an additional node type that
must be either ``gcode`` (for GCODE commands to be sent to the printer based on the event) or ``system`` (for commands to be
executed on the system OctoPrint is running on).

All event hooks can be disabled completely by setting ``event > enabled`` to ``false``. You can also disable individual
hooks by setting the (optional) node ``enabled`` to false, see the example below.

Example
-------

.. sourcecode:: yaml

   events:
     enabled: True
     subscriptions:
     - event: Disconnected
       command: python ~/growl.py -t mygrowlserver -d "Lost connection to printer" -a OctoPrint -i http://raspi/Octoprint_logo.png
       type: system
       enabled: false
     - event: PrintStarted
       command: python ~/growl.py -t mygrowlserver -d "Starting {file}" -a OctoPrint -i http://raspi/Octoprint_logo.png
       type: system
     - event: PrintDone
       command: python ~/growl.py -t mygrowlserver -d "Completed {file}" -a OctoPrint -i http://raspi/Octoprint_logo.png
       type: system
     - event: Connected
       command:
       - M115
       - M117 printer connected!
       - G28
       type: gcode

.. _sec-events-placeholders:

Placeholders
============

You can use the following generic placeholders in your event hooks:

  * ``{__currentZ}``: the current Z position of the head if known, -1 if not available
  * ``{__filename}``: filename of the currently selected file, "NO FILE" if not available
  * ``{__progress}``: the progress of the print in percent, 0 if not available
  * ``{__data}``: a string representation of the payload
  * ``{__now}``: the date and time of the event in ISO 8601

Additionally, all data from the payload can be accessed by its key. Example: If the payload happens to be defined
something like this:

  * ``file``: the file's name
  * ``origin``: the origin of the file, either ``local`` or ``sdcard``

then you'll be able to access the filename via the placeholder ``{file}`` and the origin via the placeholder ``{origin}``.

.. _sec-events-available_events:

Available Events
================

Server
------

Startup
   The server has started

ClientOpened
   A client has connected to the web server.

   Payload:

     * ``remoteAddress``: the remote address (IP) of the client that connected

   **Note:** Name changed in version 1.1.0

ClientClosed
   A client has disconnected from the webserver

   Payload:

     * ``remoteAddress``: the remote address (IP) of the client that disconnected

Printer communication
---------------------

Connected
   The server has connected to the printer.

   Payload:

     * ``port``: the connected serial port
     * ``baudrate``: the baud rate

Disconnected
   The server has disconnected from the printer

Error
   An error has occurred in the printer communication.

   Payload:

     * ``error``: the error string

File handling
-------------

Upload
   A file has been uploaded.

   Payload:
     * ``file``: the file's name
     * ``target``: the target to which the file was uploaded, either ``local`` or ``sdcard``

UpdatedFiles
   A file list was modified.

   Payload:

     * ``type``: the type of file list that was modified. Currently only ``printables`` and ``gcode`` (DEPRECATED) are supported here.

       .. note::

          The type ``gcode`` has been renamed to ``printables`` with the introduction of a new file management layer that
          supports STL files as first class citizens as well. For reasons of backwards compatibility the ``UpdatedFiles``
          event for printable files will be fired twice, once with ``type`` set to ``gcode``, once set to ``printables``.
          Support for the ``gcode`` type will be removed in the next release after version 1.2.0.

MetadataAnalysisStarted
   The metadata analysis of a GCODE file has started.

   Payload:

     * ``file``: the file's name

MetadataAnalaysisFinished
   The metadata analysis of a GCODE file has finished.

   Payload:

     * ``file``: the file's name
     * ``result``: the analysis result -- this is a python object currently only available for internal use

FileSelected
   A GCODE file has been selected for printing.

   Payload:

     * ``file``: the full path to the file
     * ``filename``: the file's name
     * ``origin``: the origin of the file, either ``local`` or ``sdcard``

FileDeselected
   No file is selected any more for printing.

TransferStarted
   A GCODE file transfer to SD has started.

   Payload:

     * ``local``: the file's name as stored locally
     * ``remote``: the file's name as stored on SD

   **Note:** Name changed in version 1.1.0

TransferDone
   A GCODE file transfer to SD has finished.

   Payload:

     * ``time``: the time it took for the transfer to complete in seconds
     * ``local``: the file's name as stored locally
     * ``remote``: the file's name as stored on SD

Printing
--------

PrintStarted
   A print has started.

   Payload:

     * ``file``: the file's name
     * ``origin``: the origin of the file, either ``local`` or ``sdcard``

PrintFailed
   A print failed.

   Payload:

     * ``file``: the file's name
     * ``origin``: the origin of the file, either ``local`` or ``sdcard``

PrintDone
   A print completed successfully.

   Payload:

     * ``file``: the file's name
     * ``origin``: the origin of the file, either ``local`` or ``sdcard``
     * ``time``: the time needed for the print, in seconds (float)

PrintCancelled
   The print has been cancelled via the cancel button.

   Payload:

     * ``file``: the file's name
     * ``origin``: the origin of the file, either ``local`` or ``sdcard``

PrintPaused
   The print has been paused.

   Payload:

     * ``file``: the file's name
     * ``origin``: the origin of the file, either ``local`` or ``sdcard``

PrintResumed
   The print has been resumed.

   Payload:

     * ``file``: the file's name
     * ``origin``: the origin of the file, either ``local`` or ``sdcard``

GCODE processing
----------------

PowerOn
   The GCode has turned on the printer power via M80

PowerOff
   The GCODE has turned on the printer power via M81

Home
   The head has gone home via G28

ZChange
   The printer's Z-Height has changed (new layer)

Paused
   The print has been paused

Waiting
   The print is paused due to a gcode wait command

Cooling
   The GCODE has enabled the platform cooler via M245

Alert
   The GCODE has issued a user alert (beep) via M300

Conveyor
   The GCODE has enabled the conveyor belt via M240

Eject
   The GCODE has enabled the part ejector via M40

EStop
   The GCODE has issued a panic stop via M112

Timelapses
----------

CaptureStart
   A timelapse image has started to be captured.

   Payload:

     * ``file``: the name of the image file to be saved

CaptureDone
   A timelapse image has completed being captured.

   Payload:
     * ``file``: the name of the image file that was saved

MovieRendering
   The timelapse movie has started rendering.

   Payload:

     * ``gcode``: the GCODE file for which the timelapse would have been created (only the filename without the path)
     * ``movie``: the movie file that is being created (full path)
     * ``movie_basename``: the movie file that is being created (only the file name without the path)

MovieDone
   The timelapse movie is completed.

   Payload:

     * ``gcode``: the GCODE file for which the timelapse would have been created (only the filename without the path)
     * ``movie``: the movie file that has been created (full path)
     * ``movie_basename``: the movie file that has been created (only the file name without the path)

MovieFailed
   There was an error while rendering the timelapse movie.

   Payload:

     * ``gcode``: the GCODE file for which the timelapse would have been created (only the filename without the path)
     * ``movie``: the movie file that would have been created (full path)
     * ``movie_basename``: the movie file that would have been created (only the file name without the path)
     * ``returncode``: the return code of ``ffmpeg`` that indicates the error that occurred

Slicing
-------

SlicingStarted
   The slicing of a file has started.

   Payload:

     * ``stl``: the STL's filename
     * ``gcode``: the sliced GCODE's filename
     * ``progressAvailable``: true if progress information via the ``slicingProgress`` push update will be available, false if not

SlicingDone
   The slicing of a file has completed.

   Payload:

     * ``stl``: the STL's filename
     * ``gcode``: the sliced GCODE's filename
     * ``time``: the time needed for slicing, in seconds (float)

SlicingCancelled
   The slicing of a file has been cancelled. This will happen if a second slicing job
   targeting the same GCODE file has been started by the user.

   Payload:

     * ``stl``: the STL's filename
     * ``gcode``: the sliced GCODE's filename

SlicingFailed
   The slicing of a file has failed.

   Payload:

     * ``stl``: the STL's filename
     * ``gcode``: the sliced GCODE's filename
     * ``reason``: the reason for the slicing having failed

Settings
--------

SettingsUpdated
   The internal settings were updated.

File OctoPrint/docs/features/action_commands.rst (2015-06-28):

.. _sec-features-action_commands:

Action Commands
===============

Action commands are a feature defined for the GCODE based RepRap communication protocol. To quote from the
`GCODE node of the RepRap wiki <http://reprap.org/wiki/Gcode#Replies_from_the_RepRap_machine_to_the_host_computer>`_:

    The RepRap machine may also send lines that look like this:

    **// This is some debugging or other information on a line on its own. It may be sent at any time.**

    Such lines will always be preceded by //.

    On the latest version of Pronterface and [...] OctoPrint a special comment of the form:

    **// action:command**

    is allowed to be sent from the firmware[. T]he command can currently be pause, resume or disconnect which will
    execute those commands on the host. As this is also a comment other hosts will just ignored these commands.

OctoPrint out of the box supports handling of the above mentioned commands:

pause
    When this command is received from the printer, OctoPrint will pause streaming of a current print job just like if the
    "Pause" button had been clicked.

resume
    When this command is received from the printer, OctoPrint will resume streaming of a current print job just like if
    the "Resume" button had been clicked.

disconnect
    When this command is Received from the printer, OctoPrint will immediately disconnect from it.

Support for additional commands may be added by plugins by implementing a handler for the
:ref:`octoprint.comm.protocol.action <sec-plugins-hook-comm-protocol-action>` hook.

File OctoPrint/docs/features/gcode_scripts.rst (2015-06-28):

.. _sec-features-gcode_scripts:

GCODE Scripts
=============

.. contents::

OctoPrint allows you to define custom GCODE scripts to be executed on specified occasions, e.g. when a print
starts, when OctoPrint connects to a printer, or when a :ref:`button defined as a custom control <sec-features-custom_controls>`
is clicked.

Unless :ref:`configured otherwise <sec-configuration-config_yaml-folder>`, OctoPrint expects scripts to be located in
the ``scripts/gcode`` folder in OctoPrint configuration directory (per default ``~/.octoprint`` on Linux, ``%APPDATA%\OctoPrint``
on Windows and ``~/Library/Application Support/OctoPrint`` on MacOS).

These GCODE scripts are backed by the templating engine `Jinja2 <http://jinja.pocoo.org/>`_, allowing more than just
simple "send-as-is" scripts but making use of a full blown templating language in order to create your scripts. To
this end, OctoPrint injects a couple of variables into the :ref:`template rendering context <sec-features-gcode_scripts-context>`
as described below.

.. _sec-features-gcode_scripts-predefined:

Predefined Scripts
------------------

The following GCODE scripts are sent by OctoPrint automatically:

  * ``afterPrinterConnected``: Sent after OctoPrint successfully connected to a printer. Defaults to an empty script.
  * ``beforePrintStarted``: Sent just before a print job is started. Defaults to an empty script.
  * ``afterPrintCancelled``: Sent just after a print job was cancelled. Defaults to the
    :ref:`bundled script listed below <sec-features-gcode_scripts-bundled>`.
  * ``afterPrintDone``: Sent just after a print job finished. Defaults to an empty script.
  * ``afterPrintPaused``: Sent just after a print job was paused. Defaults to an empty script.
  * ``beforePrintResumed``: Sent just before a print job is resumed. Defaults to an empty script.

.. note::

   Plugins may extend these scripts through :ref:`a hook <sec-plugins-hook-comm-protocol-scripts>`.

.. _sec-features-gcode_scripts-snippets:

Snippets
--------

For making small GCODE snippets reusable in a template (e.g. for :ref:`disabling all hotends <sec-features-gcode_scripts-bundled>`)
there's an additional Jinja template command ``{% snippet '<snippet name>' %}`` available which allows including
snippets stored under ``scripts/gcode/snippets`` in OctoPrint's configuration directory. They fully support
the whole spectrum of the Jinja2 templating language (that includes including other snippets).

.. _sec-features-gcode_scripts-context:

Context
-------

All GCODE scripts have access to the following template variables through the template context:

  * ``printer_profile``: The currently selected Printer Profile, including
    information such as the extruder count, the build volume size, the filament diameter etc.
  * ``script``: An object wrapping the script's type (``gcode``) and name (e.g. ``afterPrintCancelled``) as ``script.type``
    and ``script.name`` respectively.

The :ref:`predefined GCODE scripts <sec-features-gcode_scripts-predefined>` are also called with the following additional
template variables:

  * ``event``: The payload of the ``Connected``, ``PrintStarted``, ``PrintCancelled``, ``PrintDone``, ``PrintPaused`` or
    ``PrintResumed`` event. See :ref:`the documentation of events <sec-events-available_events>` for the contained values.

GCODE scripts attached to :ref:`custom controls <sec-features-custom_controls>` are called with the following
additional template variables:

  * ``parameters``: The parameters as defined for the custom control, if it has any inputs.
  * ``context``: Additional ``context`` included in the definition of the custom control.

.. _sec-features-gcode_scripts-bundled:

Bundled Scripts
---------------

Out of the box, OctoPrint defaults to the following script setup for ``afterPrintCancelled``:

.. code-block:: jinja
   :caption: Default ``afterPrintCancelled`` script

   ; disable motors
   M84

   ;disable all heaters
   {% snippet 'disable_hotends' %}
   M140 S0

   ;disable fan
   M106 S0

The ``disable_hotends`` snippet is defined as follows:

.. code-block:: jinja
   :caption: Default ``disable_hotends`` snippet

   {% for tool in range(printer_profile.extruder.count) %}
   M104 T{{ tool }} S0
   {% endfor %}

As you can see, the ``disable_hotends`` snippet utilizes the ``printer_profile`` context variable in order to
iterate through all available extruders and set their temperature to 0.

.. seealso::

   `Jinja Template Designer Documentation <http://jinja.pocoo.org/docs/dev/templates/>`_
      Jinja's Template Designer Documentation describes the syntax and semantics of the template language used
      also by OctoPrint's GCODE scripts.

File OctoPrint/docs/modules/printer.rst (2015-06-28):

.. _sec-modules-printer:

octoprint.printer
-----------------

.. automodule:: octoprint.printer

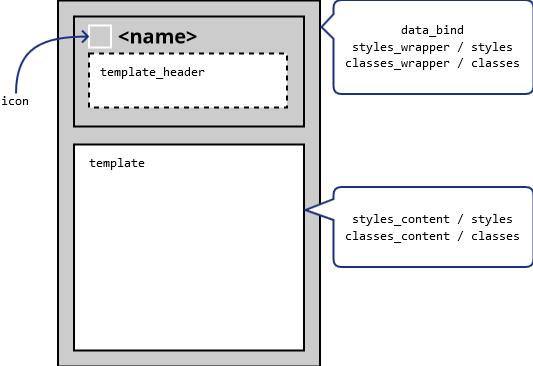
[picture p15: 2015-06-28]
OctoPrint/docs/images/template-plugin-type-sidebar.png

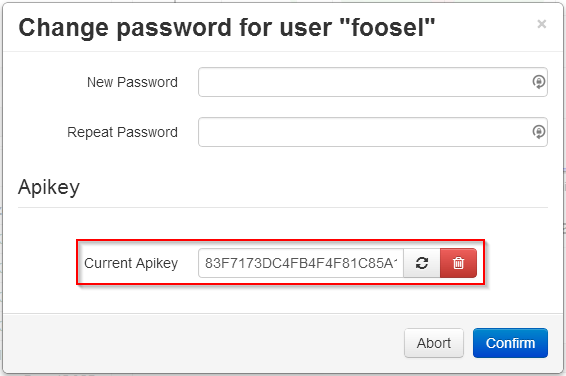
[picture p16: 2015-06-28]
OctoPrint/docs/images/change-password-api-key.png

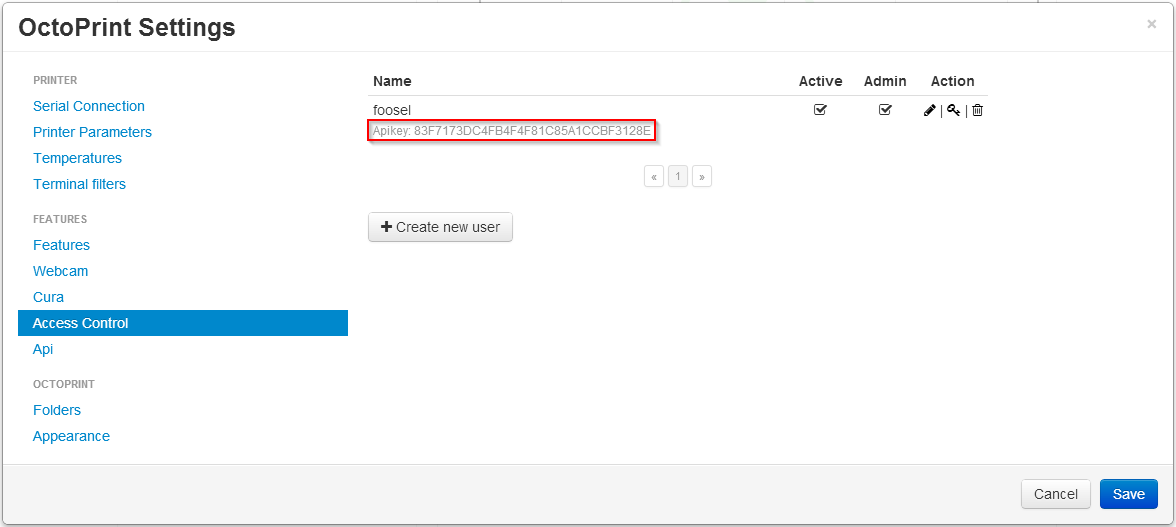
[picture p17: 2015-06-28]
OctoPrint/docs/images/settings-user-api-key.png

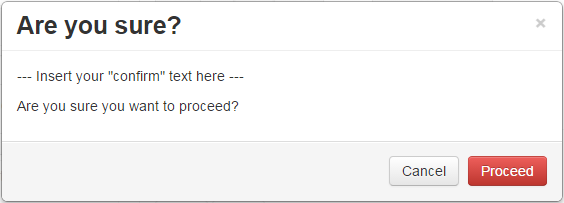
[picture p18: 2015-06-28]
OctoPrint/docs/images/features-custom_controls-confirm.png

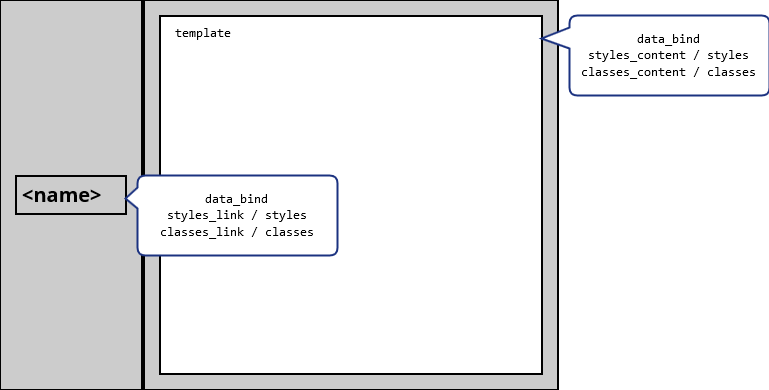
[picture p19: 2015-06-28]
OctoPrint/docs/images/template-plugin-type-settings.png

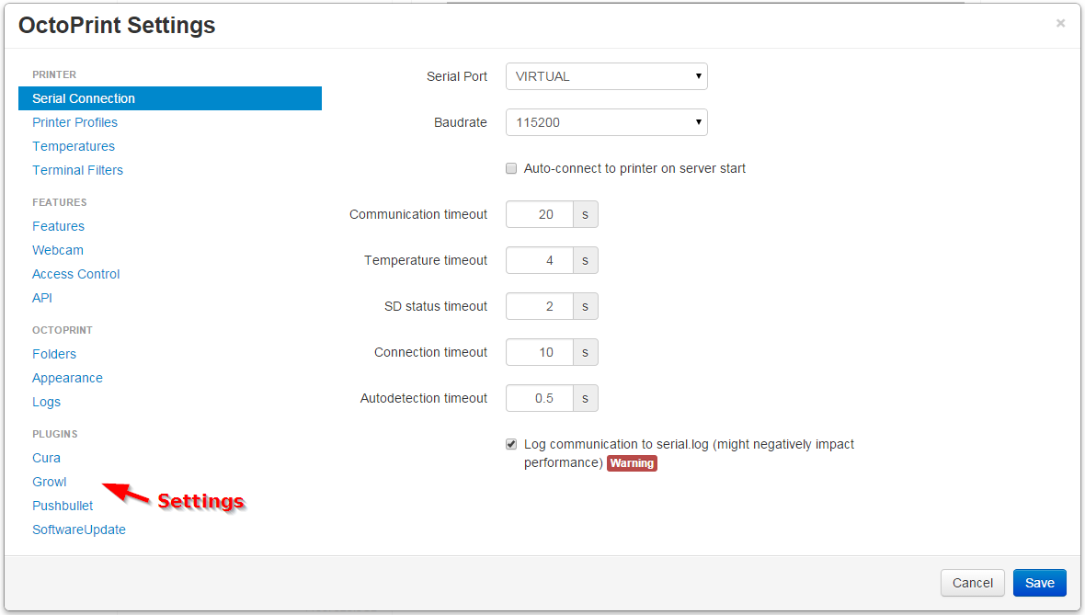
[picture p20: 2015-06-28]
OctoPrint/docs/images/template-plugin-types-settings.png

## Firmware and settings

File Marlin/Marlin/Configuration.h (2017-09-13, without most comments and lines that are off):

#define CONFIGURATION_H
#include "boards.h"
#ifdef HAS_AUTOMATIC_VERSIONING
  #include "_Version.h"
#else
  #include "Default_Version.h"
#endif
#define STRING_CONFIG_H_AUTHOR "Andrea Ambrosini (Rossonet)" // Who made the changes.
#define STRING_SPLASH_LINE1 BUILD_VERSION "Rossonet"// will be shown during bootup in line 1
#define STRING_SPLASH_LINE2 STRING_DISTRIBUTION_DATE "Atom Machine"// will be shown during bootup in line 2
#define SERIAL_PORT 0
#define BAUDRATE 250000
  #define MOTHERBOARD BOARD_MEGATRONICS_3
#define CUSTOM_MACHINE_NAME "Rossonet Atom Machine"
#define MACHINE_UUID "8f37445a-81b1-41d2-9626-f9b002295828"
#define EXTRUDERS 1
#define POWER_SUPPLY 1
#define TEMP_SENSOR_0 -1
#define TEMP_SENSOR_1 0
#define TEMP_SENSOR_2 0
#define TEMP_SENSOR_3 0
#define TEMP_SENSOR_BED 0
#define MAX_REDUNDANT_TEMP_SENSOR_DIFF 10
#define TEMP_RESIDENCY_TIME 10  // (seconds)
#define TEMP_HYSTERESIS 3       // (degC) range of +/- temperatures considered "close" to the target one
#define TEMP_WINDOW     1       // (degC) Window around target to start the residency timer x degC early.
#define HEATER_0_MINTEMP 5
#define HEATER_1_MINTEMP 5
#define HEATER_2_MINTEMP 5
#define HEATER_3_MINTEMP 5
#define BED_MINTEMP 5
#define HEATER_0_MAXTEMP 275
#define HEATER_1_MAXTEMP 275
#define HEATER_2_MAXTEMP 275
#define HEATER_3_MAXTEMP 275
#define BED_MAXTEMP 150
#define PIDTEMP
#define BANG_MAX 255 // limits current to nozzle while in bang-bang mode; 255=full current
#define PID_MAX BANG_MAX // limits current to nozzle while PID is active (see PID_FUNCTIONAL_RANGE below); 255=full current
  #define PID_FUNCTIONAL_RANGE 10 // If the temperature difference between the target temperature and the actual temperature
  #define PID_INTEGRAL_DRIVE_MAX PID_MAX  //limit for the integral term
  #define K1 0.95 //smoothing factor within the PID
  #define  DEFAULT_Kp 57.15
  #define  DEFAULT_Ki 6.92
  #define  DEFAULT_Kd 117.98
#define MAX_BED_POWER 255 // limits duty cycle to bed; 255=full current
#define PREVENT_DANGEROUS_EXTRUDE
#define PREVENT_LENGTHY_EXTRUDE
#define EXTRUDE_MINTEMP 190
#define EXTRUDE_MAXLENGTH (X_MAX_LENGTH+Y_MAX_LENGTH) //prevent extrusion of very large distances.
#define THERMAL_PROTECTION_HOTENDS // Enable thermal protection for all extruders
#define THERMAL_PROTECTION_BED     // Enable thermal protection for the heated bed
#define DELTA
  #define DELTA_SEGMENTS_PER_SECOND 200
  #define DELTA_DIAGONAL_ROD 404.0 // mm
  #define DELTA_SMOOTH_ROD_OFFSET 256.49 // mm
  #define DELTA_EFFECTOR_OFFSET 30.0 // mm
  #define DELTA_CARRIAGE_OFFSET 27.0 // mm
  #define DELTA_RADIUS (DELTA_SMOOTH_ROD_OFFSET-DELTA_EFFECTOR_OFFSET-DELTA_CARRIAGE_OFFSET)
  #define DELTA_PRINTABLE_RADIUS 114
#define ENDSTOPPULLUPS // Comment this out (using // at the start of the line) to disable the endstop pullup resistors
const bool X_MIN_ENDSTOP_INVERTING = true; // set to true to invert the logic of the endstop.
const bool Y_MIN_ENDSTOP_INVERTING = true; // set to true to invert the logic of the endstop.
const bool Z_MIN_ENDSTOP_INVERTING = true; // set to true to invert the logic of the endstop.
const bool X_MAX_ENDSTOP_INVERTING = true; // set to true to invert the logic of the endstop.
const bool Y_MAX_ENDSTOP_INVERTING = true; // set to true to invert the logic of the endstop.
const bool Z_MAX_ENDSTOP_INVERTING = true; // set to true to invert the logic of the endstop.
const bool Z_PROBE_ENDSTOP_INVERTING = true; // set to true to invert the logic of the endstop.
#define DISABLE_MIN_ENDSTOPS // Deltas only use min endstops for probing
#define X_ENABLE_ON 0
#define Y_ENABLE_ON 0
#define Z_ENABLE_ON 0
#define E_ENABLE_ON 0//For all extruders
#define DISABLE_X false
#define DISABLE_Y false
#define DISABLE_Z false
#define DISABLE_E false // For all extruders
#define DISABLE_INACTIVE_EXTRUDER true //disable only inactive extruders and keep active extruder enabled
#define INVERT_X_DIR false // DELTA does not invert
#define INVERT_Y_DIR false
#define INVERT_Z_DIR false
#define INVERT_E0_DIR true
#define INVERT_E1_DIR true
#define INVERT_E2_DIR true
#define INVERT_E3_DIR true
#define X_HOME_DIR 1  // deltas always home to max
#define Y_HOME_DIR 1
#define Z_HOME_DIR 1
#define min_software_endstops true // If true, axis won't move to coordinates less than HOME_POS.
#define max_software_endstops true  // If true, axis won't move to coordinates greater than the defined lengths below.
#define X_MIN_POS -DELTA_PRINTABLE_RADIUS
#define Y_MIN_POS -DELTA_PRINTABLE_RADIUS
#define Z_MIN_POS 0
#define X_MAX_POS DELTA_PRINTABLE_RADIUS
#define Y_MAX_POS DELTA_PRINTABLE_RADIUS
#define Z_MAX_POS MANUAL_Z_HOME_POS
#define ENABLE_AUTO_BED_LEVELING // Delete the comment to enable (remove // at the start of the line)
  #define AUTO_BED_LEVELING_GRID  // Deltas only support grid mode
    #define DELTA_PROBABLE_RADIUS 120
    #define LEFT_PROBE_BED_POSITION -79
    #define RIGHT_PROBE_BED_POSITION 79
    #define FRONT_PROBE_BED_POSITION -79
    #define BACK_PROBE_BED_POSITION 79
    #define MIN_PROBE_EDGE 10 // The probe square sides can be no smaller than this
    #define AUTO_BED_LEVELING_GRID_POINTS 5
  #define X_PROBE_OFFSET_FROM_EXTRUDER -0     // Probe on: -left  +right
  #define Y_PROBE_OFFSET_FROM_EXTRUDER 10   // Probe on: -front +behind
  #define Z_PROBE_OFFSET_FROM_EXTRUDER -10.5  // -below (always!)
  #define Z_RAISE_BEFORE_HOMING 6       // (in mm) Raise Z before homing (G28) for Probe Clearance.
  #define XY_TRAVEL_SPEED 8000         // X and Y axis travel speed between probes, in mm/min
  #define Z_RAISE_BEFORE_PROBING 60   //How much the extruder will be raised before traveling to the first probing point.
  #define Z_RAISE_BETWEEN_PROBINGS 15  //How much the extruder will be raised when traveling from between next probing points
  #define Z_RAISE_AFTER_PROBING 50    //How much the extruder will be raised after the last probing point.
  #define PROBE_SERVO_DEACTIVATION_DELAY 900
  #define Z_PROBE_ENDSTOP
#define MANUAL_HOME_POSITIONS  // If defined, MANUAL_*_HOME_POS below will be used
  #define MANUAL_X_HOME_POS 0
  #define MANUAL_Y_HOME_POS 0
  #define MANUAL_Z_HOME_POS 510.0 // For delta: Distance between nozzle and print surface after homing.
#define HOMING_FEEDRATE {50*60, 50*60, 50*60, 0}  // set the homing speeds (mm/min)
#define DEFAULT_AXIS_STEPS_PER_UNIT   {76, 76, 76, 100}  // default steps per unit for Kossel (GT2, 20 tooth)
#define DEFAULT_MAX_FEEDRATE          {500, 500, 500, 25}    // (mm/sec)
#define DEFAULT_MAX_ACCELERATION      {8000,8000,8000,3000}    // X, Y, Z, E maximum start speed for accelerated moves. E default values are good for skeinforge 40+, for older versions raise them a lot.
#define DEFAULT_ACCELERATION          2000    // X, Y, Z and E acceleration in mm/s^2 for printing moves
#define DEFAULT_RETRACT_ACCELERATION  3000    // E acceleration in mm/s^2 for retracts
#define DEFAULT_TRAVEL_ACCELERATION   2000    // X, Y, Z acceleration in mm/s^2 for travel (non printing) moves
#define DEFAULT_XYJERK                15.0    // (mm/sec)
#define DEFAULT_ZJERK                 15.0    // (mm/sec) Must be same as XY for delta
#define DEFAULT_EJERK                 4.0     // (mm/sec)
#define CUSTOM_M_CODES
    #define CUSTOM_M_CODE_SET_Z_PROBE_OFFSET 851
    #define Z_PROBE_OFFSET_RANGE_MIN -25
    #define Z_PROBE_OFFSET_RANGE_MAX -2
#define EEPROM_SETTINGS
  #define EEPROM_CHITCHAT // Please keep turned on if you can.
#define PLA_PREHEAT_HOTEND_TEMP 200
#define PLA_PREHEAT_HPB_TEMP 70
#define PLA_PREHEAT_FAN_SPEED 100   // Insert Value between 0 and 255
#define ABS_PREHEAT_HOTEND_TEMP 240
#define ABS_PREHEAT_HPB_TEMP 100
#define ABS_PREHEAT_FAN_SPEED 150   // Insert Value between 0 and 255
#define LANGUAGE_INCLUDE GENERATE_LANGUAGE_INCLUDE(it)
  #define DISPLAY_CHARSET_HD44780_JAPAN        // this is the most common hardware
#define SDSUPPORT // Enable SD Card Support in Hardware Console
#define SOFT_PWM_SCALE 0
#define NUM_SERVOS 1 // Servo index starts with 0 for M280 command
#define SERVO_ENDSTOPS {-1, -1, 0} // Servo index for X, Y, Z. Disable with -1
#define SERVO_ENDSTOP_ANGLES {0,0, 0,0, 18,82} // X,Y,Z Axis Extend and Retract angles
#define FILAMENT_SENSOR_EXTRUDER_NUM 0   //The number of the extruder that has the filament sensor (0,1,2)
#define MEASUREMENT_DELAY_CM        14   //measurement delay in cm.  This is the distance from filament sensor to middle of barrel
#define DEFAULT_NOMINAL_FILAMENT_DIA 3.00  //Enter the diameter (in mm) of the filament generally used (3.0 mm or 1.75 mm) - this is then used in the slicer software.  Used for sensor reading validation
#define MEASURED_UPPER_LIMIT         3.30  //upper limit factor used for sensor reading validation in mm
#define MEASURED_LOWER_LIMIT         1.90  //lower limit factor for sensor reading validation in mm
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

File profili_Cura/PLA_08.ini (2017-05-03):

[profile]
layer_height = 0.2
wall_thickness = 1.6
retraction_enable = True
solid_layer_thickness = 3
fill_density = 8
nozzle_size = 0.8
print_speed = 40
print_temperature = 120
print_temperature2 = 0
print_temperature3 = 0
print_temperature4 = 0
print_bed_temperature = 70
support = Everywhere
platform_adhesion = Brim
support_dual_extrusion = Both
wipe_tower = False
wipe_tower_volume = 15
ooze_shield = False
filament_diameter = 1.75
filament_diameter2 = 0
filament_diameter3 = 0
filament_diameter4 = 0
filament_flow = 100
retraction_speed = 80
retraction_amount = 2.5
retraction_dual_amount = 16.5
retraction_min_travel = 2
retraction_combing = True
retraction_minimal_extrusion = 0.1
retraction_hop = 0.1
bottom_thickness = 0.2
layer0_width_factor = 110
object_sink = 0.0
overlap_dual = 0.15
travel_speed = 70
bottom_layer_speed = 25
infill_speed = 50
inset0_speed = 35
insetx_speed = 40
cool_min_layer_time = 4
fan_enabled = True
skirt_line_count = 1
skirt_gap = 3.0
skirt_minimal_length = 150.0
fan_full_height = 1
fan_speed = 30
fan_speed_max = 70
cool_min_feedrate = 20
cool_head_lift = True
solid_top = True
solid_bottom = True
fill_overlap = 10
support_type = Grid
support_angle = 45
support_fill_rate = 5
support_xy_distance = 2
support_z_distance = 0.35
spiralize = False
simple_mode = False
brim_line_count = 12
raft_margin = 5.0
raft_line_spacing = 3.0
raft_base_thickness = 0.3
raft_base_linewidth = 1.0
raft_interface_thickness = 0.27
raft_interface_linewidth = 0.4
raft_airgap_all = 0.0
raft_airgap = 0.22
raft_surface_layers = 2
raft_surface_thickness = 0.27
raft_surface_linewidth = 0.4
fix_horrible_union_all_type_a = True
fix_horrible_union_all_type_b = False
fix_horrible_use_open_bits = False
fix_horrible_extensive_stitching = False
plugin_config = (lp1
	.
object_center_x = -1
object_center_y = -1

[alterations]
start.gcode = ;Basic settings: Layer height: {layer_height} Walls: {wall_thickness} Fill: {fill_density}
	;Print time: {print_time}
	;Filament used: {filament_amount}m {filament_weight}g
	;Filament cost: {filament_cost}
	;M190 S{print_bed_temperature} ;Uncomment to add your own bed temperature line
	;M109 S{print_temperature} ;Uncomment to add your own temperature line
	G21
	G28
	G92 E0
	M117 Pulizia estrusore...
	;Scarica filo a 220
	M107
	G1 X-114 Y-114 Z45 F9000
	M109 T0 S220
	G1 F100 E50
	G1 F400 E48
	G1 Z150 F500
	G1 X0 Y0 Z280 F9000
	G28
	M117 Calibrazione...
	G29
	G90        ;absolute positioning
	G1 X-114 Y-114 Z25 F6000
	G1 F200 E55              ;extrude 5mm of feed stock
	G92 E0                  ;zero the extruded length again
	G1 F{travel_speed}
	;Put printing message on LCD screen
	M117 Stampa...
	M104 S215
end.gcode = M104 S0
	M140 S0                     ;heated bed heater off (if you have it)
	G1 X-114 Y-114 F3000
	G91
	G1 E-1.5 F300
	M106
	G1 Z+5.5 F3000               ;retract the filament a bit before lifting the nozzle, to release some of the pressure
	G28   ;move to endstops
	M84                         ;steppers off
	G90                         ;absolute positioning
	M107
start2.gcode = 
	;Basic settings: Layer height: {layer_height} Walls: {wall_thickness} Fill: {fill_density}
	;Print time: {print_time}
	;Filament used: {filament_amount}m {filament_weight}g
	;Filament cost: {filament_cost}
	;M190 S{print_bed_temperature} ;Uncomment to add your own bed temperature line
	;M104 S{print_temperature} ;Uncomment to add your own temperature line
	;M109 T1 S{print_temperature2} ;Uncomment to add your own temperature line
	;M109 T0 S{print_temperature} ;Uncomment to add your own temperature line
	G21        ;metric values
	G90        ;absolute positioning
	M107       ;start with the fan off
	G28   ;move to endstops
	T1                      ;Switch to the 2nd extruder
	G92 E0                  ;zero the extruded length
	G1 F200 E10             ;extrude 10mm of feed stock
	G92 E0                  ;zero the extruded length again
	G1 F200 E-{retraction_dual_amount}
	T0                      ;Switch to the first extruder
	G92 E0                  ;zero the extruded length
	G1 F200 E10             ;extrude 10mm of feed stock
	G92 E0                  ;zero the extruded length again
	G1 F{travel_speed}
	;Put printing message on LCD screen
	M117 Printing...
end2.gcode = 
	M104 T0 S0                     ;extruder heater off
	M104 T1 S0                     ;extruder heater off
	M140 S0                     ;heated bed heater off (if you have it)
	G91                                    ;relative positioning
	G1 E-1 F300                            ;retract the filament a bit before lifting the nozzle, to release some of the pressure
	G1 Z+0.5 E-5 X-20 Y-20 F{travel_speed} ;move Z up a bit and retract filament even more
	G28   ;move to endstops
	M84                         ;steppers off
	G90                         ;absolute positioning
start3.gcode = ;Sliced at: {day} {date} {time}
	;Basic settings: Layer height: {layer_height} Walls: {wall_thickness} Fill: {fill_density}
	;Print time: {print_time}
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

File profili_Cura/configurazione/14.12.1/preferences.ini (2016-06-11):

[preference]
startmode = Normal
oneatatime = True
lastfile = /home/andrea/git/liberamente/porco.stl
save_profile = False
filament_cost_kg = 35
filament_cost_meter = 0
auto_detect_sd = True
check_for_updates = True
submit_slice_information = True
youmagine_token = 
filament_physical_density = 1240
language = English
active_machine = 0
model_colour = #FFC924
model_colour2 = #CB3030
model_colour3 = #DDD93C
model_colour4 = #4550D3
printing_window = Basic
window_maximized = True
window_pos_x = -1
window_pos_y = -1
window_width = -1
window_height = -1
window_normal_sash = 320
last_run_version = 14.12.1

[machine_0]
machine_name = RAM
machine_type = reprap
machine_width = 228
machine_depth = 228
machine_height = 420
machine_center_is_zero = True
machine_shape = Circular
ultimaker_extruder_upgrade = False
has_heated_bed = False
gcode_flavor = RepRap (Marlin/Sprinter)
extruder_amount = 1
extruder_offset_x1 = 0.0
extruder_offset_y1 = 21.6
extruder_offset_x2 = 0.0
extruder_offset_y2 = 0.0
extruder_offset_x3 = 0.0
extruder_offset_y3 = 0.0
steps_per_e = 0
serial_port = AUTO
serial_port_auto = 
serial_baud = AUTO
serial_baud_auto = 
extruder_head_size_min_x = 8
extruder_head_size_min_y = 8
extruder_head_size_max_x = 8
extruder_head_size_max_y = 8
extruder_head_size_height = 10

[machine_1]
machine_name = Arduino Materia101
machine_type = RepRap
machine_width = 140
machine_depth = 100
machine_height = 200
machine_center_is_zero = False
machine_shape = Square
ultimaker_extruder_upgrade = False
has_heated_bed = True
gcode_flavor = RepRap (Marlin/Sprinter)
extruder_amount = 1
extruder_offset_x1 = 0.0
extruder_offset_y1 = 21.6
extruder_offset_x2 = 0.0
extruder_offset_y2 = 0.0
extruder_offset_x3 = 0.0
extruder_offset_y3 = 0.0
steps_per_e = 0
serial_port = AUTO
serial_port_auto = 
serial_baud = AUTO
serial_baud_auto = 
extruder_head_size_min_x = 0.0
extruder_head_size_min_y = 0.0
extruder_head_size_max_x = 0.0
extruder_head_size_max_y = 0.0
extruder_head_size_height = 0.0

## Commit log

2015-05-30 Trasferimento da http://git.rossonet.net/gitblit-1.2.1/summary/Ar4kPrinter.git
    [20mm_xy.stl, Belt-Tensioner-V1.0.scad, Belt-Tensioner-V1.0.stl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]
2015-06-01 Riordino cartella
    [Belt-Tensioner-V1.0.scad, Belt-Tensioner-V1.0.stl, Configuration.h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]
2015-06-05 puntatore laser e telecamera
    [Belt-Tensioner-V1.0.scad, Linear_Bearing.scad, belt_coupler_v6_Mod.scad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]
2015-06-07 aggiunti gcode scrittura
    [Geng_final_sup.stl]
2015-06-07 Aggiornamento parametri marlin -pre tuning-
    [Configuration.h]
2015-06-07 Nuova blocco penna
    [supporto_giotto_turbocolor.scad, supporto_giotto_turbocolor.stl]
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2015-06-08 calibrazione step per unità in marlin
    [Configuration.h]
2015-06-08 aggiunti alcuni gcode per calibrazione
    [20mm_xy.stl, elfgirl_support_V1.stl, stecche.scad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]
2015-06-09 calibrazione nuova altezza e area di stampa
    [Configuration.h]
2015-06-09 aggiornamento area stampabile
    [Configuration.h]
2015-06-09 nuovi gcode e configurazione pronterface
    [20mm_xy.stl]
2015-06-09 zggiornamento gcode
    [piattaforma_test.scad, supporto_borletti.scad, supporto_borletti.stl]
2015-06-17 Riorganizzati file oggetti
    [Belt-Tensioner-V1.0.scad, Letters.dxf, Linear_Bearing.scad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]
2015-06-19 Aggiunto estrusore e supporto hotend
    [hotend.scad, piattaforma_3dprint.scad, piattaforma_3dprint_coperchio.stl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]
2015-06-21 Primo gcode stampa 3d
    [10cm.scad, 10cm.stl, piattaforma_3dprint.scad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]
2015-06-21 Aggiornamento z_home dopo z-probe
    [Configuration.h]
2015-06-22 Aggiunto assemblaggio
    [carrello.scad, piattaforma_3dprint.scad, ram.scad]
2015-06-22 aggiornamento gcode
    [10cm.scad, 10cm.stl]
2015-06-26 Aggiunto gcode e proconsole conf nuovo
    [Configuration.h]
2015-06-26 nuove parti
    [9g_servo.scad, attuatore_siringa.scad, nemaMount.scad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]
2015-06-27 prime prove autoprobe piano
    [Configuration.h]
2015-06-27 implementato g30
    [Configuration.h]
2015-06-27 test su g29
    [Configuration.h, Configuration_adv.h]
2015-06-27 correzione grid g29
    [Configuration.h]
2015-06-28 test debug g28
    [Configuration.h, Configuration_adv.h]
2015-06-28 tolto quickhome
    [Configuration_adv.h]
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2015-06-28 Incluso OctoPrint
    [babel.cfg, bp_case.stl, crazyradio.stl]
2015-06-28 Incluso OctoPrint conf
    [configurazioneOctoprint.txt]
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2015-07-03 Piano a un centesimo
    [Configuration.h, configurazioneOctoprint.txt]
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2015-07-07 primo disegno estrusore con refrattario
    [piattaforma_3dprint.scad, piattaforma_3dprint_v2.scad, piattaforma_3dprint_v2_coperchio_a.stl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]
2015-07-08 Attuatore 3d print v2
    [Configuration.h, configurazioneOctoprint.txt]
2015-07-08 Configurazione attuatore stampa v2
    [punti_rilevamento.scad]
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2015-07-09 Primo test stampa 3D passato
    [10cm.scad, 10cm.stl, elfgirl_support_V1.stl]
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2015-07-12 Stampa PLA a 100mm/s
    [Configuration.h, Configuration_adv.h, configurazioneOctoprint.txt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]
2015-07-12 Profili Cura a 100mm/s
    [3d_sculpture-VernonBussler.stl, Amf_Cube.amf, CurveEdgeTest.amf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]
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2015-07-15 Stampa PLA a 70mm/s
    [configurazioneOctoprint.txt]
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2015-07-18 Nuovo attuatore stampa additiva
    [Configuration.h, configurazioneOctoprint.txt]
2015-07-20 Stampa in PLA completata
    [configurazioneOctoprint.txt]
2015-07-22 Link OpenJScad in OctoPrint
    [configurazioneOctoprint.txt]
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2015-09-20 riduzione ventola in profili Cura
    [configurazioneOctoprint.txt]
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2015-09-24 Correzione fattore di correzione temperatura
    [Configuration_adv.h, blocco_motore.scad]
2015-09-24 Correzione incremento di correzione temperatura
    [Configuration_adv.h, blocco_motore.scad]
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2015-09-24 Aggiornamento parametri controllo temperatura
    [Configuration_adv.h, blocco_motore.scad]
2015-09-24 base e testa nuovi
    [piede.scad]
2015-09-25 versione beta in preparazione
    [Configuration_adv.h]
2015-09-25 Profili per versione beta completati
    [10cm.scad, 10cm.stl, Configuration.h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]
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2015-09-29 Correzione temperatura nuova termocoppia
    [Configuration_adv.h]
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2015-10-01 Correzione piede dopo prototipo
    [piede.scad]
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2016-01-13 aggiunto script configurazione git
    [bananas-gda-pl.stl]
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2017-04-07 implementazione G667 e varie
    [Configuration.h, Configuration_adv.h, carrello.scad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]
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2017-04-20 Varie modifiche RAM, aggiunta progetto robot polare e sestante nei modelli di test
    [2xBraccia.STL, 2xFCE.1501.02.005_smooth_drivegear.STL, 2xbraccia_v2.stl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]
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2017-06-10 aggiunti file Prusa i3
    [Prusa3WOOD-v4.dxf, Prusa3_SC10UU-v1.dxf, bearing-guide.scad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]
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2017-08-07 Aggiunta configurazione attuale RAM
    [configurazioneOctoprintRam.txt]
2017-08-07 Configurazione Wasp 2040 in laboratorio
    [configurazioneOctoprintWasp2040.txt]
2017-08-07 Aggiornata configurazione Materia 101
    [configurazioneOctoprintRam.txt]
2017-08-07 script compilazione e caricamento
    [Prusa3WOOD-v4.dxf, Prusa3_SC10UU-v1.dxf, bearing-guide.scad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]
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2017-09-13 Nuova configurazione G667 e G668
    [Configuration.h, FCE.1501.01.001_hub_r01.STL, FCE.1501.01.003_ring.STL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]

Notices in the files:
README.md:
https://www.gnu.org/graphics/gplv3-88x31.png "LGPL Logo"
